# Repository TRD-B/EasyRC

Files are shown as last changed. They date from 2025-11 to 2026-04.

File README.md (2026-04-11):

# EasyRC - open-source RC platform

EasyRC vehicle

Description
---
EasyRC is an easy-to-build platform for creating your own remote-controlled vehicle. The platform includes CAD files for printing an affordable 1:16 scale car as well as a small remote control. Further, it includes the project and production files for the printed circuit boards that are needed to power these devices. Last but not least, it lists all required components in a bill of materials and comes with a complete instruction manual that shows how to print, solder, assemble, program, and adjust everything for running the car. The legacy folder contains data and information from previous revisions of the project.

The idea of this platform is to serve as a starting point for people who are interested in DIY hobby electronics as well as 3D printing, but were reluctant so far due to the initial burdens that are associated with the complexity of these topics. Hence, EasyRC offers a simple start for beginners, but due to its open-source character, it offers full freedom to tweak, redesign, and reprogram all parts of the project.

The 1:16 scale vehicle is designed for indoor use (for the sake of simplicity, it does not encompass suspension) and can be safely operated by kids (maximum speed is 10 km/h but can be set lower within the software). Hence, the project is also a great gift for kids who want to dive into engineering and programming topics, or start with driving a selfmade remote-controlled car and look behind the scenes once they're getting older.

The manual is available in English and German.

Specifications
---
Vehicle:
- Size: 282x125x95 mm³ (LxWxH)
- Scale: 1:16
- Weight: approx. 1 kg (including batteries)
- Microcontroller: ESP32-C3
- Wireless communication: 2.4 GHz (ESP-NOW protocol)
- Motor driver: Pololu DRV8876 (QFN)
- Drive motor: JGA25-370 Brushed DC motor with gearbox (12 V, 1000 U/min)
- Speed: max. 10 km/h
- Steering servo: MG90S metal-gear micro servo
- Power supply: 3x 18650 Li-Ion battery (11.1 V)
- Power consumption: approx. 0.8 W (idle); approx. 3-6 W (driving)

Remote control:
- Size: 80x40x41 mm³ (LxWxH)
- Weight: approx. 125 g (including battery)
- Microcontroller: ESP32-C3
- Wireless communication: 2.4 GHz (ESP-NOW protocol)
- Joystick: Alps 10k (Playstation 4 model)
- Power supply: 1x 18650 Li-Ion battery (3.7 V)
- Power consumption: approx. 0.5 W

Safety information:
---
- Voltage levels are 12 V or less (harmless for humans)
-	Battery connectors are reverse polarity protected
-	Low battery warnings are included
-	The motor automatically stops if the connection to the remote control is lost

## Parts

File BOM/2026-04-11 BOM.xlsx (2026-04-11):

Component | Description | Amount needed | Pieces per unit | Required units | Costs per unit | Costs per piece | Scaled price | Total cost | Link
Motor | Brushed 370 with 1:10 gearbox | 1 | 1 | 1 | 8.49 € | 8.49 € | 8.49 € | 8.49 € | https://www.amazon.de/dp/B07ZKKN226?
Servo | MG90S metal gear micro servo | 1 | 1 | 1 | 4.00 € | 4.00 € | 4.00 € | 4.00 € | https://funduinoshop.com/elektronische-module/elektromotoren-und-zubehoer/elektromotoren/servomotoren/mg90s-metallgetriebe-micro-servo
Battery holder | 3x18650 | 1 | 1 | 1 | 1.87 € | 1.87 € | 1.87 € | 1.87 € | https://funduinoshop.com/werkstatt/stromversorgung/batteriefaecher-und-klemmen/batterriefach-fuer-3x-3-7v-18650-batterien-11-7v-mit-kabel
Battery holder | 1x18650 | 1 | 1 | 1 | 1.06 € | 1.06 € | 1.06 € | 1.06 € | https://funduinoshop.com/werkstatt/stromversorgung/batteriefaecher-und-klemmen/batteriefach-1x-18650-li-ionen-zelle
Battery | Lishen 18650 3.1 Ah | 4 | 10 | 1 | 26.50 € | 2.65 € | 10.60 € | 26.50 € | https://www.pollin.de/p/liion-akku-lishen-lr1865ss-3-6v-3-1ah-273545
Microcontroller | Xiao ESP32-C3 | 2 | 1 | 2 | 5.90 € | 5.90 € | 11.80 € | 11.80 € | https://botland.de/wifi-und-bt-module-esp32/21859-seeed-xiao-esp32-c3-wlan-bluetooth-seeedstudio-113991054.html
On/off switch | Marquardt 1801.1148 | 1 | 1 | 1 | 1.80 € | 1.80 € | 1.80 € | 1.80 € | https://www.reichelt.de/de/de/shop/produkt/wippschalter_ein_-_aus_1_polig_schwarz-257132
On/off switch | Miniature slide switch | 1 | 1 | 1 | 0.48 € | 0.48 € | 0.48 € | 0.48 € | https://www.reichelt.de/de/de/shop/produkt/schiebeschalter-miniatur_loetanschluss_2x_um_sw-19976
Fuse | PTC, ESKA FRG300-16F | 1 | 1 | 1 | 0.47 € | 0.47 € | 0.47 € | 0.47 € | https://www.voelkner.de/products/2682/ESKA-FRG300-16F-FRG300-16F-PTC-Sicherung-Strom-I-H-3A-16V-L-x-B-x-H-7.8-x-3.0-x-19.3mm.html
DC-DC converter | TSR1-2450E | 1 | 1 | 1 | 3.28 € | 3.28 € | 3.28 € | 3.28 € | https://www.voelkner.de/products/3510672/TracoPower-TSR-1-2450E-DC-DC-Wandler-Print-1A-5W-Anzahl-Ausgaenge-1-x-Inhalt-1St..html
Capacitor | Electrolytic, 100µF 25V 6.3mm pitch 2.5mm | 2 | 1 | 2 | 0.25 € | 0.25 € | 0.50 € | 0.50 € | https://www.reichelt.de/de/de/shop/produkt/elko_radial_100_uf_25_v_105_c_low_esr-200027
Capacitor | Electrolytic, 22µF 25V 5mm pitch 2.5mm | 1 | 1 | 1 | 0.25 € | 0.25 € | 0.25 € | 0.25 € | https://www.reichelt.de/de/de/shop/produkt/elko_radial_22_f_25_v_105_c_low_esr_5_x_7_mm_rm_2_5-84588
Buzzer | PB1220PE05Q | 1 | 1 | 1 | 0.50 € | 0.50 € | 0.50 € | 0.50 € | https://www.reichelt.de/de/de/shop/produkt/ac-signalgeber_85db_2048_hz_5_v-360862?search=pb1220&
LED | 5 mm, white | 2 | 1 | 2 | 0.08 € | 0.08 € | 0.16 € | 0.16 € | https://www.reichelt.de/de/de/shop/produkt/led_5_mm_bedrahtet_kaltweiss_15000_mcd_25_-347932
LED | 5 mm, yellow | 4 | 1 | 4 | 0.08 € | 0.08 € | 0.32 € | 0.32 € | https://www.reichelt.de/de/de/shop/produkt/led_5_mm_bedrahtet_gelb_700_mcd_30_-347921
LED | 5 mm, red | 2 | 1 | 2 | 0.08 € | 0.08 € | 0.16 € | 0.16 € | https://www.reichelt.de/de/de/shop/produkt/led_5_mm_bedrahtet_rot_700_mcd_30_-347922
LED | 5 mm, green | 1 | 1 | 1 | 0.08 € | 0.08 € | 0.08 € | 0.08 € | https://www.reichelt.de/de/de/shop/produkt/led_5_mm_bedrahtet_gruen_2500_mcd_30_-347919
Motor driver | Pololu DRV8876 QFN | 1 | 1 | 1 | 6.50 € | 6.50 € | 6.50 € | 6.50 € | https://botland.de/motortreiber-module/21361-drv8876-qfn-einkanal-treiber-37-v-11-a-pololu-4037.html
MOSFET | IRLU 024N | 6 | 1 | 6 | 0.46 € | 0.46 € | 2.76 € | 2.76 € | https://www.reichelt.de/de/de/shop/produkt/mosfet_n-ch_55v_17a_0_065r_to-251aa-90365
Zener diode | Semtech ZD 8.2 | 1 | 1 | 1 | 0.05 € | 0.05 € | 0.05 € | 0.05 € | https://www.reichelt.de/de/de/shop/produkt/zenerdiode_8_2_v_1_w_do-204al_do41-23101
Schottky diode | 1N 5817 | 1 | 1 | 1 | 0.10 € | 0.10 € | 0.10 € | 0.10 € | https://www.reichelt.de/de/de/shop/produkt/schottkydiode_20_v_1_a_do-41-376347
Resistor | 330Ohm 0207 | 1 | 1 | 1 | 0.07 € | 0.07 € | 0.07 € | 0.07 € | https://www.reichelt.de/de/de/shop/produkt/widerstand_metallschicht_330_ohm_0207_0_6_w_1_-11733
Resistor | 470Ohm 0207 | 16 | 1 | 16 | 0.07 € | 0.07 € | 1.12 € | 1.12 € | https://www.reichelt.de/de/de/shop/produkt/widerstand_metallschicht_470_ohm_0207_0_6_w_1_-11826
Resistor | 1kOhm 0207 | 4 | 1 | 1 | 0.07 € | 0.07 € | 0.28 € | 0.07 € | https://www.reichelt.de/de/de/shop/produkt/widerstand_metallschicht_1_00_kohm_0207_0_6_w_1_-11403
Resistor | 10kOhm 0207 | 1 | 1 | 1 | 0.07 € | 0.07 € | 0.07 € | 0.07 € | https://www.reichelt.de/de/de/shop/produkt/widerstand_metallschicht_10_0_kohm_0207_0_6_w_1_-11449
Resistor | 22kOhm 0207 | 3 | 1 | 1 | 0.07 € | 0.07 € | 0.21 € | 0.07 € | https://www.reichelt.de/de/de/shop/produkt/widerstand_metallschicht_22_0_kohm_0207_0_6_w_1_-11622
Resistor | 33kOhm 0207 | 2 | 1 | 2 | 0.07 € | 0.07 € | 0.14 € | 0.14 € | https://www.reichelt.de/de/de/shop/produkt/widerstand_metallschicht_33_0_kohm_0207_0_6_w_1_-11730
Resistor | 100kOhm 0207 | 2 | 1 | 1 | 0.07 € | 0.07 € | 0.14 € | 0.07 € | https://www.reichelt.de/de/de/shop/produkt/widerstand_metallschicht_100_kohm_0207_0_6_w_1_-11458
Joystick | ALPS PS4 Joystick | 1 | 1 | 1 | 2.90 € | 2.90 € | 2.90 € | 2.90 € | https://www.retroretter.de/products/as_ps4_white_alps_10k
Pin header | W+P 10-pin angled | 1 | 2 | 1 | 0.36 € | 0.18 € | 0.18 € | 0.36 € | https://www.reichelt.de/de/de/shop/produkt/stiftleiste_rm_2_54mm_gewinkelt_1-reihig_10-polig-330991
Socket strip | mpe 7-pin | 4 | 1 | 6 | 0.31 € | 0.31 € | 1.24 € | 1.86 € | https://www.reichelt.de/de/de/shop/produkt/buchsenleisten_2_54_mm_1x07_gerade-119916
Socket strip | 10-pin (5 mm height) | 2 | 1 | 1 | 0.75 € | 0.75 € | 1.50 € | 0.75 € | https://www.reichelt.de/de/de/shop/produkt/10pol_buchsenleiste_gerade_rm_2_54-6070
Pin header | mpe 1x20-pin | 5 | 5 | 1 | 0.35 € | 0.07 € | 0.35 € | 0.35 € | https://www.reichelt.de/de/de/shop/produkt/stiftleisten_2_54_mm_1x20_gerade-119888
Pin header | mpe 2x20-pin | 4 | 4 | 1 | 0.69 € | 0.17 € | 0.69 € | 0.69 € | https://www.reichelt.de/de/de/shop/produkt/stiftleisten_2_54_mm_2x20_gerade-119900
Crimp set | Dupont 610 parts | 15 | 100 | 1 | 9.75 € | 0.10 € | 1.46 € | 9.75 € | https://www.reichelt.de/de/de/shop/produkt/entwicklerboards_-_dupont-crimp-set_610-teilig-279901
Wire | 0.25 mm², black, 25m | 4 | 25 | 1 | 4.70 € | 0.19 € | 0.75 € | 4.70 € | https://www.pollin.de/p/rautronic-schaltlitze-liyv-0-25-mm2-25-m-schwarz-560118
Wire | 0.25 mm², red, 25m | 4 | 25 | 1 | 4.70 € | 0.19 € | 0.75 € | 4.70 € | https://www.pollin.de/p/rautronic-schaltlitze-liyv-0-25-mm2-25-m-rot-560048
Ball bearing | 608ZZ 8x22x7 | 4 | 50 | 1 | 9.99 € | 0.20 € | 0.80 € | 9.99 € | https://www.amazon.de/Rillenkugellager-Carbonstahl-Pr%C3%A4zisionslager-Skateboards-Rollerblades/dp/B0F28Q2LCV/
Ball bearing | 605ZZ 5x14x5 | 4 | 30 | 1 | 8.99 € | 0.30 € | 1.20 € | 8.99 € | https://www.amazon.de/QUARKZMAN-Rillenkugel-Bohrung-Karbonstahl-Abgeschirmt/dp/B0CL4XKFW7/?th=1
Ball bearing | 6802ZZ 15x24x5 | 2 | 10 | 1 | 6.72 € | 0.67 € | 1.34 € | 6.72 € | https://www.motedis.com/de/Rillenkugellager-6802-2Z-15x24x5
Filament | PETG, black | 400 | 1000 | 1 | 32.99 € | 0.03 € | 13.20 € | 32.99 € | https://www.prusa3d.com/product/prusament-petg-jet-black-1kg/
Filament | PETG, red | 250 | 1000 | 1 | 32.99 € | 0.03 € | 8.25 € | 32.99 € | https://www.prusa3d.com/product/prusament-petg-lipstick-red-1kg/
Filament | TPU, 82A | 35 | 500 | 1 | 32.99 € | 0.07 € | 2.31 € | 32.99 € | https://www.3djake.de/recreus/filaflex-black
Screw | M3x8 | 29 | 100 | 1 | 3.58 € | 0.04 € | 1.04 € | 3.58 € | https://shop.der-schraubenladen.de/DIN-912-ISO-4762-Zylinderschraube-Innensechskant-Edelstahl-A2/SW11250.70
Screw | M3x10 countersunk | 3 | 1000 | 1 | 19.35 € | 0.02 € | 0.06 € | 19.35 € | https://shop.der-schraubenladen.de/DIN-7991-ISO-10642-Senkschraube-Innensechskant-Edelstahl-A2/SW11501.23
Screw | M3x16 | 11 | 100 | 1 | 4.37 € | 0.04 € | 0.48 € | 4.37 € | https://shop.der-schraubenladen.de/DIN-912-ISO-4762-Zylinderschraube-Innensechskant-Edelstahl-A2/SW11250.74
Screw | M3x20 | 8 | 100 | 1 | 5.54 € | 0.06 € | 0.44 € | 5.54 € | https://shop.der-schraubenladen.de/DIN-912-ISO-4762-Zylinderschraube-Innensechskant-Edelstahl-A2/SW11250.76
Screw | M3x30 | 21 | 100 | 1 | 7.57 € | 0.08 € | 1.59 € | 7.57 € | https://shop.der-schraubenladen.de/DIN-912-ISO-4762-Zylinderschraube-Innensechskant-Edelstahl-A2/SW11250.79
Hex nut | M3 | 64 | 500 | 1 | 10.76 € | 0.02 € | 1.38 € | 10.76 € | https://shop.der-schraubenladen.de/DIN-934-ISO-4032-Sechskantmutter-Edelstahl-A2/SW11410.19
PCB | JLCPCB | 1 | 5 | 1 | 8.00 € | 1.60 € | 1.60 € | 8.00 € | https://jlcpcb.com/
PCB | JLCPCB | 1 | 5 | 1 | 8.00 € | 1.60 € | 1.60 € | 8.00 € | https://jlcpcb.com/
 |  |  |  |  |  |  | Scaled | Prototype
Total costs |  |  |  |  |  |  | 102.37 € | 290.64 €

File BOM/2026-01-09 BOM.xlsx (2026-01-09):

Component | Description | Amount needed | Pieces per unit | Required units | Costs per unit | Costs per piece | Scaled price | Total cost | Link
Motor | Brushed 370 with 1:10 gearbox | 1 | 1 | 1 | 8.49 | 8.49 | 8.49 | 8.49 | https://www.amazon.de/dp/B07ZKKN226?
Servo | MG90S metal gear micro servo | 1 | 1 | 1 | 4 | 4 | 4 | 4 | https://funduinoshop.com/elektronische-module/elektromotoren-und-zubehoer/elektromotoren/servomotoren/mg90s-metallgetriebe-micro-servo
Battery holder | 3x18650 | 1 | 1 | 1 | 1.87 | 1.87 | 1.87 | 1.87 | https://funduinoshop.com/werkstatt/stromversorgung/batteriefaecher-und-klemmen/batterriefach-fuer-3x-3-7v-18650-batterien-11-7v-mit-kabel
Battery holder | 1x18650 | 1 | 1 | 1 | 1.06 | 1.06 | 1.06 | 1.06 | https://funduinoshop.com/werkstatt/stromversorgung/batteriefaecher-und-klemmen/batteriefach-1x-18650-li-ionen-zelle
Battery | Lishen 18650 3.1 Ah | 4 | 10 | 1 | 26.5 | 2.65 | 10.6 | 26.5 | https://www.pollin.de/p/liion-akku-lishen-lr1865ss-3-6v-3-1ah-273545
Microcontroller | Xiao ESP32-C3 | 2 | 1 | 2 | 5.9 | 5.9 | 11.8 | 11.8 | https://botland.de/wifi-und-bt-module-esp32/21859-seeed-xiao-esp32-c3-wlan-bluetooth-seeedstudio-113991054.html
On/off switch | Marquardt 1801.1148 | 1 | 1 | 1 | 1.8 | 1.8 | 1.8 | 1.8 | https://www.reichelt.de/de/de/shop/produkt/wippschalter_ein_-_aus_1_polig_schwarz-257132
On/off switch | Miniature slide switch | 1 | 1 | 1 | 0.48 | 0.48 | 0.48 | 0.48 | https://www.reichelt.de/de/de/shop/produkt/schiebeschalter-miniatur_loetanschluss_2x_um_sw-19976
Fuse | PTC, 1.5A | 1 | 1 | 1 | 0.76 | 0.76 | 0.76 | 0.76 | https://www.reichelt.de/de/de/shop/produkt/ptc-sicherung_smd_1812_24v_1_5a_rueckstellend-279366
DC-DC converter | TSR1-2450E | 1 | 1 | 1 | 3.99 | 3.99 | 3.99 | 3.99 | https://www.reichelt.de/de/de/shop/produkt/dc_dc_converter_tsr_1e_1_a_7-36_5_0_vdc_sip-3-288648
Capacitor | Electrolytic, 100µF 25V 6.3mm pitch 2.5mm | 2 | 1 | 2 | 0.25 | 0.25 | 0.5 | 0.5 | https://www.reichelt.de/de/de/shop/produkt/elko_radial_100_uf_25_v_105_c_low_esr-200027
Buzzer | PB1220PE05Q | 1 | 1 | 1 | 0.5 | 0.5 | 0.5 | 0.5 | https://www.reichelt.de/de/de/shop/produkt/ac-signalgeber_85db_2048_hz_5_v-360862?search=pb1220&
LED | 5 mm, white | 2 | 1 | 2 | 0.08 | 0.08 | 0.16 | 0.16 | https://www.reichelt.de/de/de/shop/produkt/led_5_mm_bedrahtet_kaltweiss_15000_mcd_25_-347932
LED | 5 mm, yellow | 4 | 1 | 4 | 0.08 | 0.08 | 0.32 | 0.32 | https://www.reichelt.de/de/de/shop/produkt/led_5_mm_bedrahtet_gelb_700_mcd_30_-347921
LED | 5 mm, red | 2 | 1 | 2 | 0.08 | 0.08 | 0.16 | 0.16 | https://www.reichelt.de/de/de/shop/produkt/led_5_mm_bedrahtet_rot_700_mcd_30_-347922
LED | 5 mm, green | 1 | 1 | 1 | 0.08 | 0.08 | 0.08 | 0.08 | https://www.reichelt.de/de/de/shop/produkt/led_5_mm_bedrahtet_gruen_2500_mcd_30_-347919
Motor driver | Pololu DRV8876 QFN | 1 | 1 | 1 | 6.5 | 6.5 | 6.5 | 6.5 | https://botland.de/motortreiber-module/21361-drv8876-qfn-einkanal-treiber-37-v-11-a-pololu-4037.html
MOSFET | IRLML6344 | 6 | 1 | 6 | 0.25 | 0.25 | 1.5 | 1.5 | https://www.reichelt.de/de/de/shop/produkt/mosfet_n-ch_30v_5a_0_029r_sot-23-132147
Zener diode | CDIL SMD ZD 8.2 | 1 | 1 | 1 | 0.04 | 0.04 | 0.04 | 0.04 | https://www.reichelt.de/de/de/shop/produkt/zenerdiode_8_2_v_0_35_w_sot-23-18926
Capacitor | ceramic, 22µF 10V 1206 | 2 | 1 | 2 | 0.26 | 0.26 | 0.52 | 0.52 | https://www.reichelt.de/de/de/shop/produkt/smd-vielschichtkondensator_g1206_-_22_f_10v-89742
Capacitor | ceramic 100nF 50V 0805 | 1 | 1 | 1 | 0.03 | 0.03 | 0.03 | 0.03 | https://www.reichelt.de/de/de/shop/produkt/smd-kerko_0805_100_nf_50v_10_x7r_mlcc-346808
Resistor | 330Ohm 0805 | 1 | 1 | 1 | 0.02 | 0.02 | 0.02 | 0.02 | https://www.reichelt.de/de/de/shop/produkt/smd-widerstand_0805_220_ohm_125_mw_1_-346599
Resistor | 470Ohm 0805 | 16 | 1 | 16 | 0.02 | 0.02 | 0.32 | 0.32 | https://www.reichelt.de/de/de/shop/produkt/smd-widerstand_0805_470_ohm_125_mw_1_-346619
Resistor | 1kOhm 0805 | 4 | 1 | 1 | 0.02 | 0.02 | 0.08 | 0.02 | https://www.reichelt.de/de/de/shop/produkt/smd-widerstand_0805_1_kohm_125_mw_1_-346593
Resistor | 22kOhm 0805 | 3 | 1 | 1 | 0.02 | 0.02 | 0.06 | 0.02 | https://www.reichelt.de/de/de/shop/produkt/smd-widerstand_0805_22_kohm_125_mw_1_-346600
Resistor | 10kOhm 0805 | 1 | 1 | 1 | 0.02 | 0.02 | 0.02 | 0.02 | https://www.reichelt.de/de/de/shop/produkt/smd-widerstand_0805_10_kohm_125_mw_1_-346579
Resistor | 33kOhm 0805 | 2 | 1 | 2 | 0.02 | 0.02 | 0.04 | 0.04 | https://www.reichelt.de/de/de/shop/produkt/smd-widerstand_0805_33_kohm_125_mw_1_-346610
Resistor | 100kOhm 0805 | 2 | 1 | 1 | 0.02 | 0.02 | 0.04 | 0.02 | https://www.reichelt.de/de/de/shop/produkt/smd-widerstand_0805_100_kohm_125_mw_1_-346577
Joystick | ALPS PS4 Joystick | 1 | 1 | 1 | 2.9 | 2.9 | 2.9 | 2.9 | https://www.retroretter.de/products/as_ps4_white_alps_10k
Pin header | W+P 10-pin angled | 1 | 2 | 1 | 0.36 | 0.18 | 0.18 | 0.36 | https://www.reichelt.de/de/de/shop/produkt/stiftleiste_rm_2_54mm_gewinkelt_1-reihig_10-polig-330991
Socket strip | mpe 7-pin | 4 | 1 | 6 | 0.31 | 0.31 | 1.24 | 1.86 | https://www.reichelt.de/de/de/shop/produkt/buchsenleisten_2_54_mm_1x07_gerade-119916
Socket strip | 10-pin (5 mm height) | 2 | 1 | 1 | 0.75 | 0.75 | 1.5 | 0.75 | https://www.reichelt.de/de/de/shop/produkt/10pol_buchsenleiste_gerade_rm_2_54-6070
Pin header | mpe 1x20-pin | 5 | 5 | 1 | 0.35 | 0.07 | 0.35 | 0.35 | https://www.reichelt.de/de/de/shop/produkt/stiftleisten_2_54_mm_1x20_gerade-119888
Pin header | mpe 2x20-pin | 4 | 4 | 1 | 0.69 | 0.1725 | 0.69 | 0.69 | https://www.reichelt.de/de/de/shop/produkt/stiftleisten_2_54_mm_2x20_gerade-119900
Jumper | 2.54 mm Jumper | 1 | 1 | 1 | 0.02 | 0.02 | 0.02 | 0.02 | https://www.reichelt.de/de/de/shop/produkt/kurzschlussbruecke_schwarz_rm_2_54-9017
Crimp set | Dupont 610 parts | 15 | 100 | 1 | 9.75 | 0.0975 | 1.4625 | 9.75 | https://www.reichelt.de/de/de/shop/produkt/entwicklerboards_-_dupont-crimp-set_610-teilig-279901
Wire | 0.25 mm², black, 25m | 4 | 25 | 1 | 4.7 | 0.188 | 0.752 | 4.7 | https://www.pollin.de/p/rautronic-schaltlitze-liyv-0-25-mm2-25-m-schwarz-560118
Wire | 0.25 mm², red, 25m | 4 | 25 | 1 | 4.7 | 0.188 | 0.752 | 4.7 | https://www.pollin.de/p/rautronic-schaltlitze-liyv-0-25-mm2-25-m-rot-560048
Ball bearing | 608ZZ 8x22x7 | 4 | 50 | 1 | 9.99 | 0.1998 | 0.7992 | 9.99 | https://www.amazon.de/Rillenkugellager-Carbonstahl-Pr%C3%A4zisionslager-Skateboards-Rollerblades/dp/B0F28Q2LCV/
Ball bearing | 605ZZ 5x14x5 | 4 | 30 | 1 | 8.99 | 0.2996666667 | 1.198666667 | 8.99 | https://www.amazon.de/QUARKZMAN-Rillenkugel-Bohrung-Karbonstahl-Abgeschirmt/dp/B0CL4XKFW7/?th=1
Ball bearing | 6802ZZ 15x24x5 | 2 | 10 | 1 | 6.72 | 0.672 | 1.344 | 6.72 | https://www.motedis.com/de/Rillenkugellager-6802-2Z-15x24x5
Filament | PETG, black | 400 | 1000 | 1 | 32.99 | 0.03299 | 13.196 | 32.99 | https://www.prusa3d.com/product/prusament-petg-jet-black-1kg/
Filament | PETG, red | 250 | 1000 | 1 | 32.99 | 0.03299 | 8.2475 | 32.99 | https://www.prusa3d.com/product/prusament-petg-lipstick-red-1kg/
Filament | TPU, 82A | 35 | 500 | 1 | 32.99 | 0.06598 | 2.3093 | 32.99 | https://www.3djake.de/recreus/filaflex-black
Screw | M3x8 | 29 | 100 | 1 | 3.58 | 0.0358 | 1.0382 | 3.58 | https://shop.der-schraubenladen.de/DIN-912-ISO-4762-Zylinderschraube-Innensechskant-Edelstahl-A2/SW11250.70
Screw | M3x10 countersunk | 3 | 1000 | 1 | 19.35 | 0.01935 | 0.05805 | 19.35 | https://shop.der-schraubenladen.de/DIN-7991-ISO-10642-Senkschraube-Innensechskant-Edelstahl-A2/SW11501.23
Screw | M3x12 | 4 | 100 | 1 | 3.9 | 0.039 | 0.156 | 3.9 | https://shop.der-schraubenladen.de/DIN-912-ISO-4762-Zylinderschraube-Innensechskant-Edelstahl-A2/SW11250.72
Screw | M3x16 | 7 | 100 | 1 | 4.37 | 0.0437 | 0.3059 | 4.37 | https://shop.der-schraubenladen.de/DIN-912-ISO-4762-Zylinderschraube-Innensechskant-Edelstahl-A2/SW11250.74
Screw | M3x20 | 6 | 100 | 1 | 5.54 | 0.0554 | 0.3324 | 5.54 | https://shop.der-schraubenladen.de/DIN-912-ISO-4762-Zylinderschraube-Innensechskant-Edelstahl-A2/SW11250.76
Screw | M3x22 | 2 | 100 | 1 | 6 | 0.06 | 0.12 | 6 | https://shop.der-schraubenladen.de/DIN-912-ISO-4762-Zylinderschraube-Innensechskant-Edelstahl-A2/SW11250.77
Screw | M3x30 | 17 | 100 | 1 | 7.57 | 0.0757 | 1.2869 | 7.57 | https://shop.der-schraubenladen.de/DIN-912-ISO-4762-Zylinderschraube-Innensechskant-Edelstahl-A2/SW11250.79
Screw | M3x35 | 2 | 100 | 1 | 8.66 | 0.0866 | 0.1732 | 8.66 | https://shop.der-schraubenladen.de/DIN-912-ISO-4762-Zylinderschraube-Innensechskant-Edelstahl-A2/SW11250.80
Screw | M3x40 | 2 | 100 | 1 | 9.69 | 0.0969 | 0.1938 | 9.69 | https://shop.der-schraubenladen.de/DIN-912-ISO-4762-Zylinderschraube-Innensechskant-Edelstahl-A2/SW11250.81
Hex nut | M3 | 64 | 500 | 1 | 10.76 | 0.02152 | 1.37728 | 10.76 | https://shop.der-schraubenladen.de/DIN-934-ISO-4032-Sechskantmutter-Edelstahl-A2/SW11410.19
PCB | JLCPCB | 1 | 5 | 1 | 8 | 1.6 | 1.6 | 8 | https://jlcpcb.com/
PCB | JLCPCB | 1 | 5 | 1 | 8 | 1.6 | 1.6 | 8 | https://jlcpcb.com/
 |  |  |  |  |  |  | Scaled | Prototype
Total costs |  |  |  |  |  |  | 100.9228967 | 317.69

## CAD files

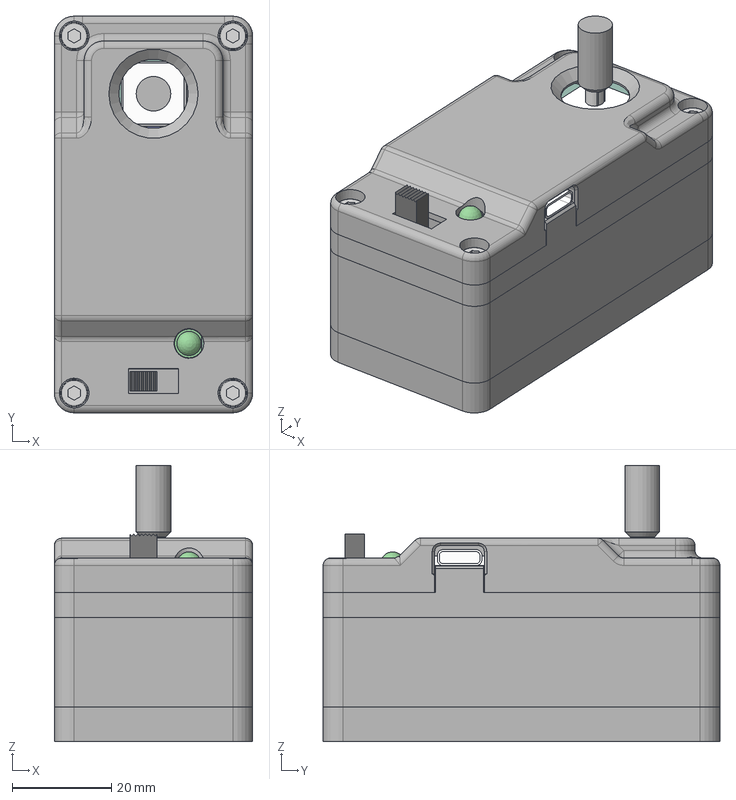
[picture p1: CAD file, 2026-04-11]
CAD files/Assembly/Easy RC remote control.step
40.0 x 80.0 x 55.6 mm
18650 1-cell holder v1
M3x10 countersunk_1
M3x8 screw_2 x 2
M3 nut_7 x 7
M3x30 screw_1 x 4
Remote control lower intermediate frame
Remote control upper intermediate frame
Remote control bottom
Remote control battery cover
Remote control joystick extension
Remote control top
R_Axial_DIN0207_L6.3mm_D2.5mm_P2.54mm_Vertical x 5
Seeed Xiao ESP32-C3
TO-251-3_Vertical
PinHeader_1x04_P2.54mm_Horizontal
PS5 Joystick
Wentronic S166 slide switch
LED_D5.0mm
Easy RC Tx V1.2_pad
Easy RC Tx V1.2_silkscreen
Easy RC Tx V1.2_soldermask
Easy RC Tx V1.2_PCB
Pin header x 2
18650 LiIon v1

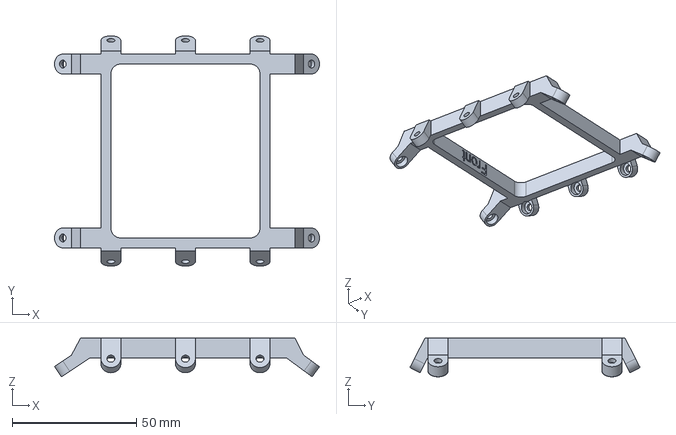
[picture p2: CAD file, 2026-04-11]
CAD files/Car/Window holder.step
106.7 x 92.7 x 15.6 mm

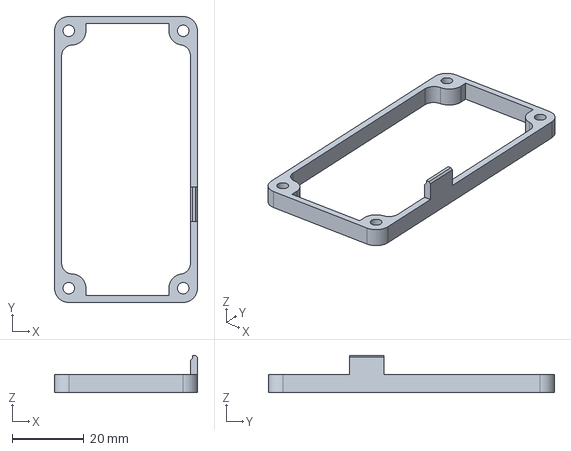
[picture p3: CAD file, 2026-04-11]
CAD files/Remote control/Remote control upper intermediate frame.step
40.0 x 80.0 x 10.4 mm

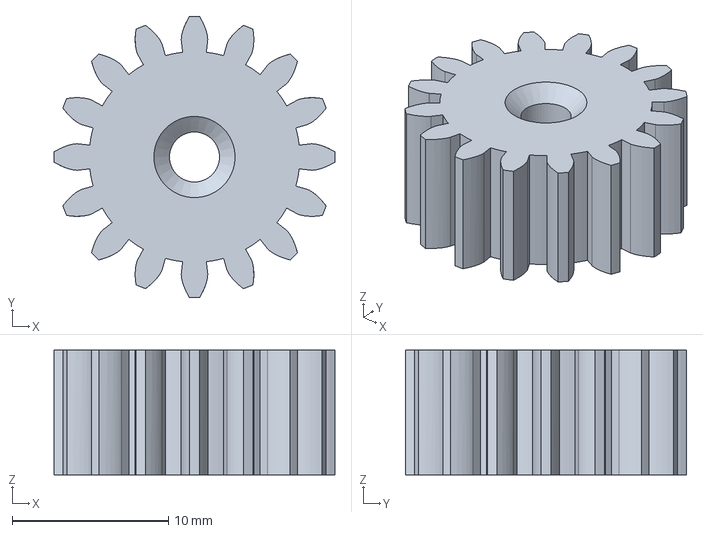
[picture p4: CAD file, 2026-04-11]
CAD files/Car/16 teeth gear.step
18.0 x 18.0 x 8.00 mm

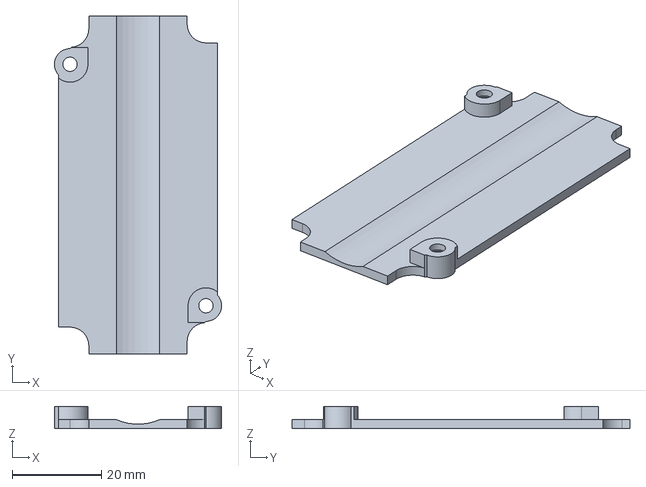
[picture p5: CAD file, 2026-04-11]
CAD files/Remote control/Remote control battery cover.step
37.4 x 75.6 x 5.00 mm

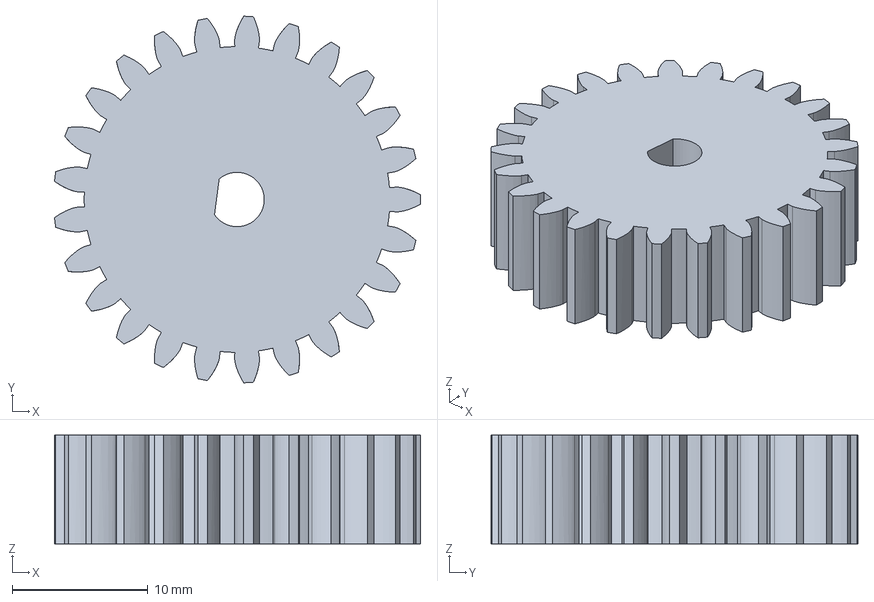
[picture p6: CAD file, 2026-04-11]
CAD files/Car/25 teeth gear.step
26.9 x 27.0 x 8.00 mm

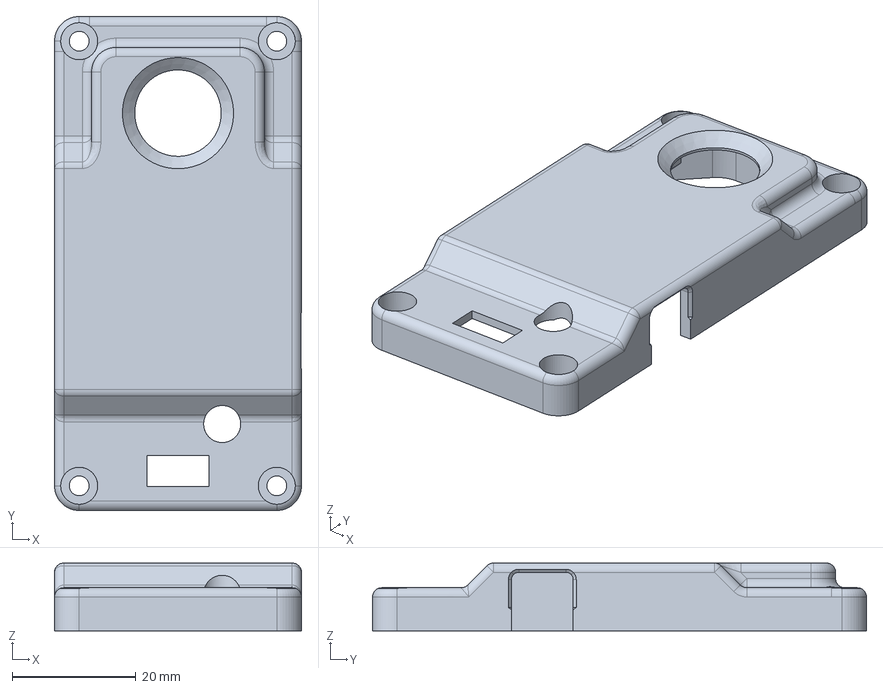
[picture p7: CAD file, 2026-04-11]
CAD files/Remote control/Remote control top.step
40.0 x 80.0 x 11.0 mm

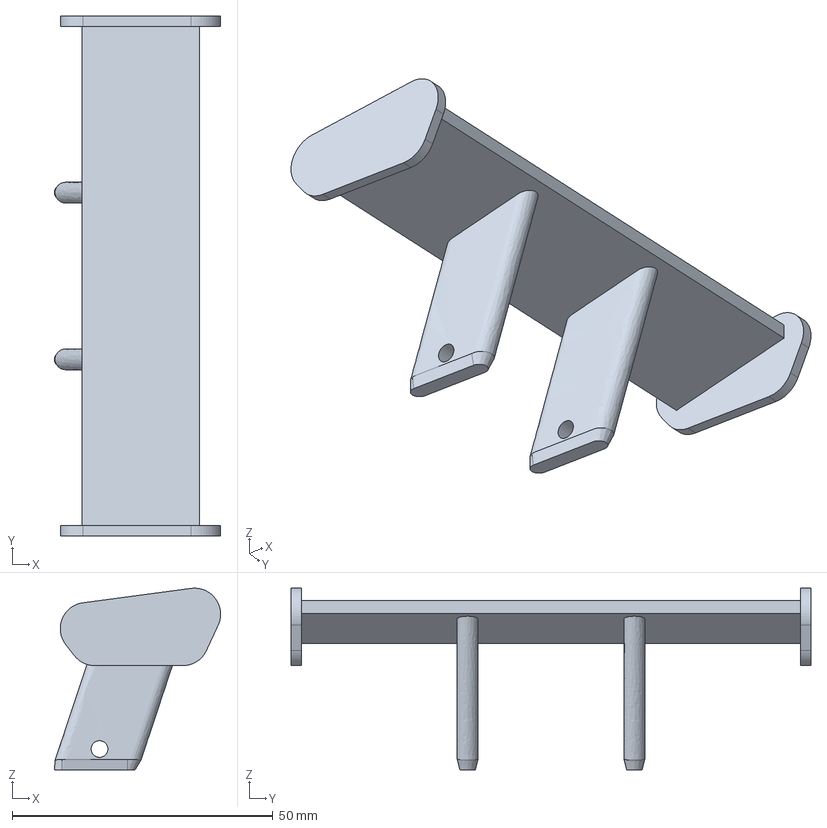
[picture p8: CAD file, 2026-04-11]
CAD files/Car/Rear wing.step
31.9 x 99.8 x 34.9 mm

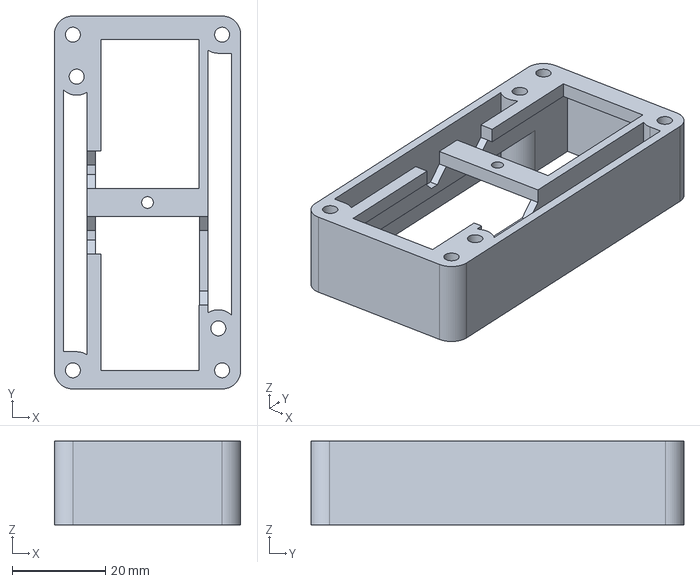
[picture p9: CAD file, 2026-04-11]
CAD files/Remote control/Remote control lower intermediate frame.step
40.0 x 80.0 x 18.0 mm

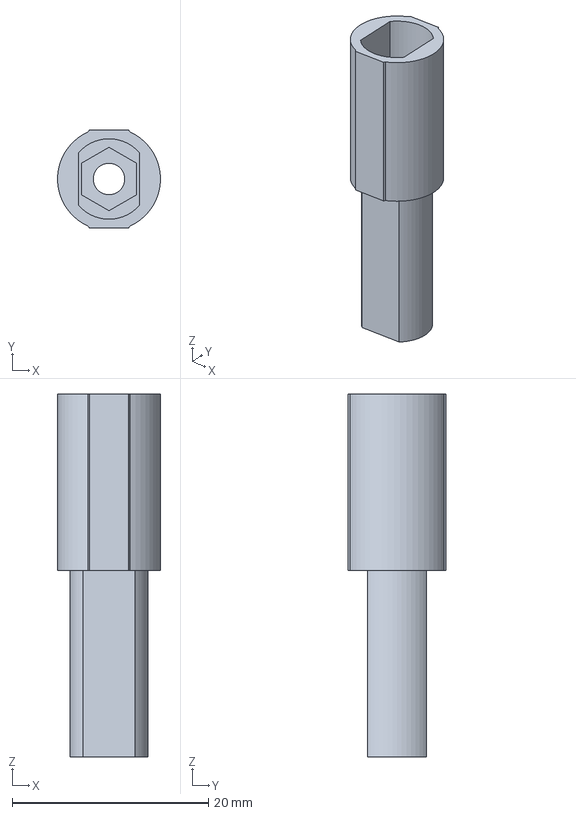
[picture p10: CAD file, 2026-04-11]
CAD files/Car/Right rear axle TPU.step
10.5 x 10.0 x 37.0 mm

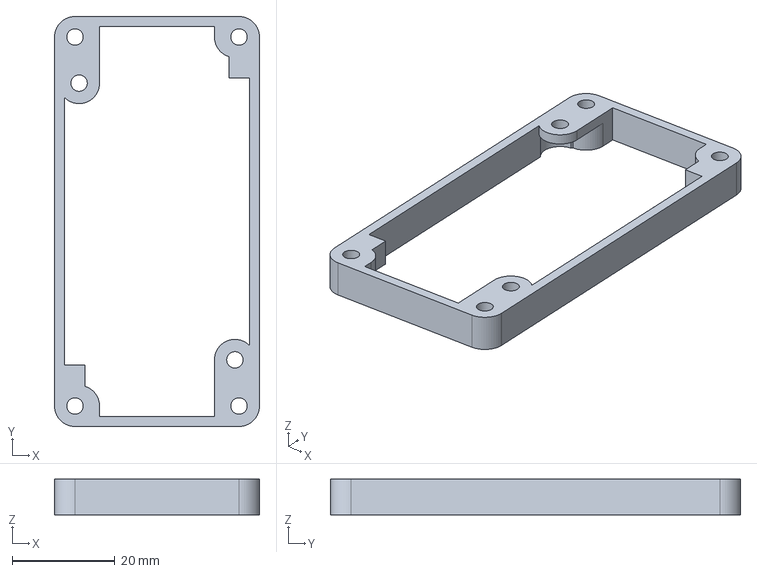
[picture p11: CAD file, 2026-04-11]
CAD files/Remote control/Remote control bottom.step
40.0 x 80.0 x 7.00 mm

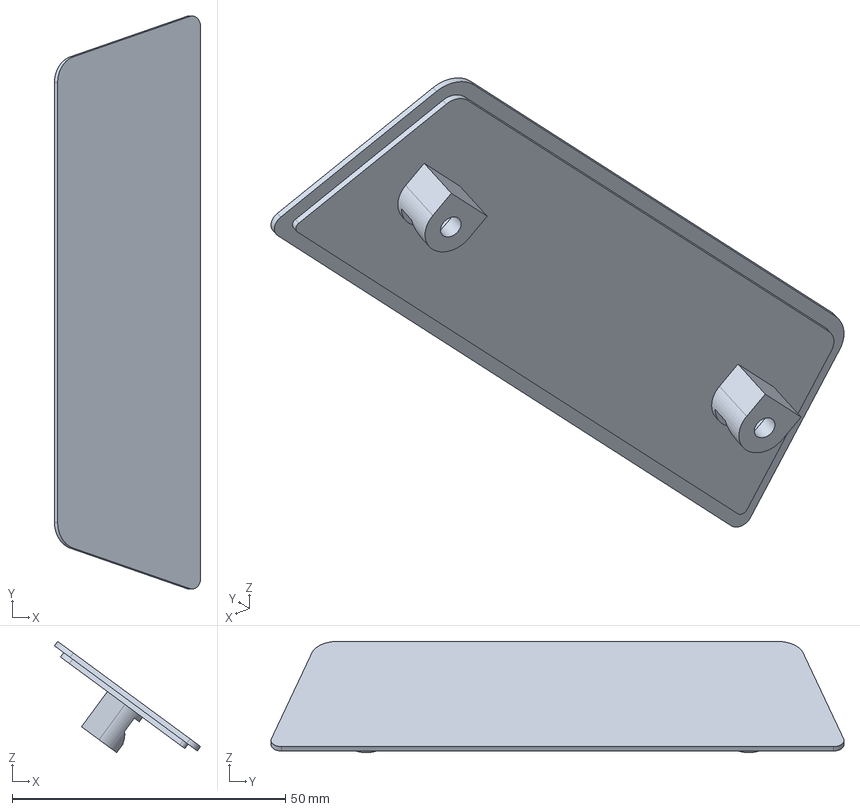
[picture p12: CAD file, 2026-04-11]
CAD files/Car/Rear window.step
26.8 x 104.9 x 20.4 mm

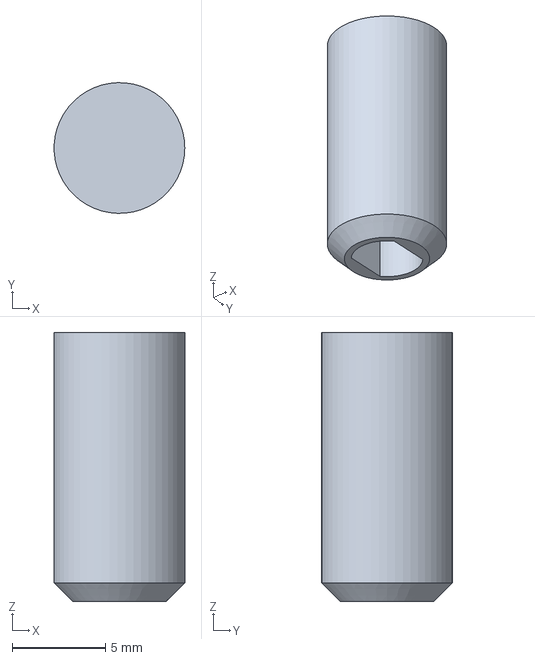
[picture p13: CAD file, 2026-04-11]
CAD files/Remote control/Remote control joystick extension.step
6.99 x 7.00 x 14.4 mm

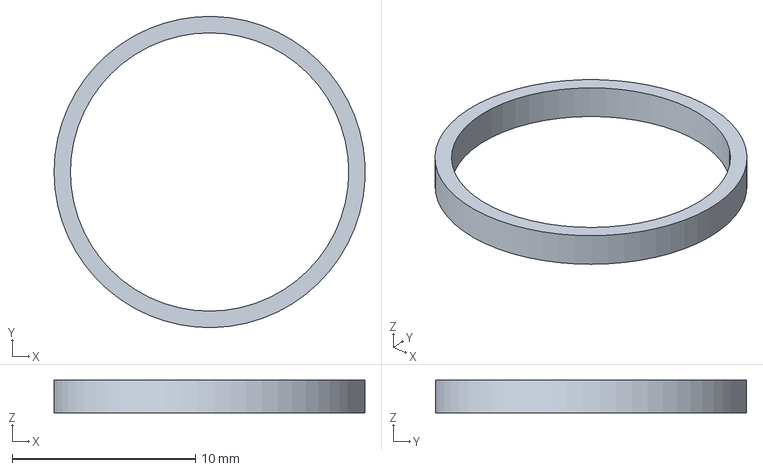
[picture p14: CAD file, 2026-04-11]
CAD files/Car/Differential spacer ring.step
17.0 x 17.0 x 1.80 mm

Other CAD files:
CAD files/Car/Right rear LED insert.step
CAD files/Car/Servo horn attachment large TPU.step
CAD files/Car/Chassis top.step
CAD files/Car/Left rear LED insert.step
CAD files/Car/10 teeth crown gear.step
CAD files/Car/10teeth crown gear.step
CAD files/Car/15 teeth crown gear.step
CAD files/Car/15teeth crown gear.step
CAD files/Car/16 teeth bearing mount.step
CAD files/Car/24 teeth gear.step
CAD files/Car/Battery lid.step
CAD files/Car/Chassis bottom.step
CAD files/Car/Chassis securing bracket.step
CAD files/Car/Differential case.step
CAD files/Car/Differential spacer.step
CAD files/Car/Front LED insert.step
CAD files/Car/Front body.step
CAD files/Car/Front bumper.step
CAD files/Car/Front light clamp.step
CAD files/Car/Front rim locking ring.step
CAD files/Car/Front rim spacer.step
CAD files/Car/Front rim.step
CAD files/Car/Front wheel mount spacer.step
CAD files/Car/Front window.step
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

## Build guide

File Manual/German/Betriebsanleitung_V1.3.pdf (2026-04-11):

# EasyRC – Open Source Fernsteuerungsplattform

## Betriebsanleitung

Version 1.3; Stand: 11.04.2026

2

## Inhaltsverzeichnis

1. Hinweise und Spezifikationen | 4
1.1 | Sicherheitshinweise | 4
1.2 | Spezifikationen der EasyRC-Plattform | 5
2. Teilelisten | 6
2.1 | Elektronikbauteile | 6
2.2 | Metallbauteile | 8
2.3 | Gedruckte Bauteile | 9
3. Elektronik | 16
3.1 | Einführung in die Elektronik | 16
3.2 | Fertigung und Bestückung der Leiterplatten | 17
3.3 | Crimpen und Verlöten der Elektronikbauteile | 18
3.4 | Komponentenliste | 19
3.5 | Übersicht Fernsteuerungselektronik | 22
3.6 | Übersicht Fahrzeugelektronik | 25
4. Bauanleitung Fernsteuerung und Fahrzeug | 31
4.1 | Fernbedienung | 35
4.2 | Antriebsstrang und Hinterräder | 41
4.3 | Vorderräder und Lenkung | 51
4.4 | Finalisierung Chassis | 58
4.5 | Karosserie | 65
5. Programmierung | 73
5.1 | Installation Arduino IDE | 73
5.2 | Mögliche und benötigte Code-Modifikationen | 75
5.3 | Programmieren der Microcontroller | 77
6. Code der Microcontroller | 79
6.1 | Fernsteuerung | 79
6.2 | Fahrzeug | 80
7. Erste Schritte und Bedienung des Fahrzeugs | 82
7.1 | Batterien einsetzen und Geräte anschalten | 82
7.2 | Lenkung fertig montieren | 83
7.3 | Fahrzeug fertig montieren | 85
7.4 | Steuerungsprinzip und Funktionen des Fahrzeugs | 86
7.5 | Trimmung der Lenkung | 87
7.6 | Feintuning der Fahreigenschaften | 88

3

8. Mögliche Fehler und Lösungsansätze | 89
9. Anhang | 90
9.1 | Änderung der Geräte-Adresse der EasyRC-Plattform | 90
9.2 | Änderung des Funkkanals der EasyRC-Plattform | 91
10. | Noch umzusetzende Verbesserungen | 92
11. | Impressum | 93

4

## 1. Hinweise und Spezifikationen

### 1.1 Sicherheitshinweise

EasyRC ist eine open-source-Plattform für drahtlos ferngesteuerte Modellfahrzeuge, die als Bausatz aus 3D-gedruckten Bauteilen montiert werden. Das Benutzerhandbuch muss vor dem Zusammenbau und der Inbetriebnahme vollständig gelesen und verstanden werden, um Gefahrenquellen zu erkennen und Verletzungen oder Schäden zu vermeiden.
Für ferngesteuerte Modellfahrzeuge gilt grundsätzlich, dass diese nicht im öentlichen Straßenverkehr bewegt werden dürfen. Bei ferngesteuerten Modellen besteht die Gefahr, dass der Steuernde die Kontrolle verliert, wenn die Drahtlosverbindung durch Überschreiten der maximalen Übertragungsreichweite oder Interferenzen gestört wird. EasyRC beinhaltet dafür eine Sicherheitsroutine, die beim Ausbleiben von Funksignalen der Fernsteuerung für wenigstens eine Sekunde die Motoren deaktiviert (die Fernsteuerung überträgt pro Sekunde 20 Datenpakete an das Modellfahrzeug, sodass diese Sicherung nicht durch einzelne verlorene Datenpakete ausgelöst werden kann). Diese Sicherheitsroutine bleibt jedoch funktionslos bei Störsignalen, die vom Modellfahrzeug fälschlicherweise als Signal der Fernsteuerung interpretiert werden. Dafür prüft das Modellfahrzeug die individuelle Geräte-Adresse (MAC) der Fernsteuerung, die mit jedem Datenpaket gesendet wird. Nur wenn diese mit der intern gespeicherten Geräte-Adresse der gekoppelten Fernsteuerung übereinstimmt, wird das Datenpaket weiterverarbeitet. Deshalb ist es beim gleichzeitigen Betrieb mehrerer EasyRC-Modelle wichtig, dass jedes mit einer anderen Geräte-Adresse programmiert wird, sodass jede Fernsteuerung spezifisch nur ein Fahrzeug steuert. Die Drahtlosverbindung basiert auf einer Funkfrequenz von 2,4 GHz, in der auch herkömmliches WLAN arbeitet. Daher besteht grundsätzlich in Häusern mit vielen verschiedenen Drahtlosnetzwerken ein erhöhtes Risiko für Verbindungsabbrüche. Sollte es zu häufigen Aussetzern kommen, kann der Sendekanal der EasyRC-Plattform geändert werden.
Die EasyRC-Plattform nutzt Batterien mit Systemspannungen von maximal ca. 12 V Gleichspannung. Diese Spannung ist ungefährlich für den Menschen; es kann zu keinen gefährlichen Stromschlägen kommen. Zudem ist die Platine des Fahrzeugs über eine Sicherung vor zu großem Stromfluss geschützt. Jedoch können Batterien bei unsachgemäßem Gebrauch (z.B. durch Überladen, Kurzschluss, mechanische Beschädigung) beschädigt werden, was zur Entzündung und zum Freisetzen gesundheitsschädlicher Inhaltsstoe führen kann. Die im Modellsystem verwendeten Lithium-Ionen-Batterien dürfen deshalb nur mit dafür geeigneten Ladegeräten aufgeladen werden. Die maximale Spannung (Ladeschlussspannung) einer einzelnen Zelle beträgt 4.2 V. Diese Spannung darf nicht überschritten werden! Die Batterien dürfen nicht weiterverwendet werden, wenn sie mechanisch beschädigt sind oder überladen worden sind. Ein Kurzschluss muss unbedingt vermieden werden. Auch eine Tiefentladung (<2.5 V) kann die Zellen irreparabel beschädigen. Die Platinen der Fernsteuerung und des Fahrzeugs sind verpolungsgeschützt. Da das Fahrzeug mit drei in Serie geschalteten Batteriezellen betrieben wird, muss beim Einsetzen der Batterien dennoch unbedingt auf die richtige Ausrichtung (Polarität) geachtet werden, um Schäden an den Batterien zu vermeiden. Batterien und Elektronikkomponenten dürfen nicht im Restmüll entsorgt werden, sondern müssen entsprechend der örtlichen Möglichkeiten umweltgerecht entsorgt bzw. recycelt werden.

5

### 1.2 Spezifikationen der EasyRC-Plattform

### 1.2.1 Fernsteuerung

Abmessungen: 80x40x41 mm³ (LxBxH)
Gewicht: ca. 125 g (inklusive Batterie)
Microcontroller: ESP32-C3
Drahtloskommunikation: 2,4 GHz (ESP-NOW Protokoll) Joystick: Alps 10k (Playstation 4 Modell) Stromversorgung: 1x 18650 Li-Ion Batterie (3,7 V) Energieverbrauch: ca. 0,5 W
Hinweise:
- Batterieanschluss verpolungsgeschützt
- Warnung bei niedriger Batteriespannung (<3,4 V): LED beginnt zu blinken
- Selbstkalibrierender Joystick

### 1.2.2 Fahrzeug

Abmessungen: 282x125x95 mm³ (LxBxH) Maßstab: 1:16
Gewicht: ca. 1 kg (inklusive Batterien)
Microcontroller: ESP32-C3
Drahtloskommunikation: 2,4 GHz (ESP-NOW Protokoll)
Motortreiber: Pololu DRV8876 (QFN)
Antriebsmotor: JGA25-370 Bürstenmotor mit Getriebe (12 V, 1000 U/min) Geschwindigkeit: max. 10 km/h
Lenkungsservo: MG90S Microservo mit Metallgetriebe Stromversorgung: 3x 18650 Li-Ion Batterie (11.1 V)
Stromverbrauch: ca. 0,8 W (Leerlauf); ca. 3-6 W (Fahrbetrieb)
Hinweise:
- Batterieanschluss verpolungsgeschützt
- Warnung bei niedriger Batteriespannung (<10,2 V): Motor deaktiviert, Buzzer piept
- Warnung bei fehlender Verbindung zur Fernsteuerung (>1 s): Motor deaktiviert, Buzzer piept
- Warnung bei ausbleibenden Nutzereingaben (kein Input für >1 min): Buzzer piept
- Selbstrückstellende Sicherung bei zu großem Stromfluss (>1.5 A)

6

## 2. Teilelisten

### 2.1 Elektronikbauteile

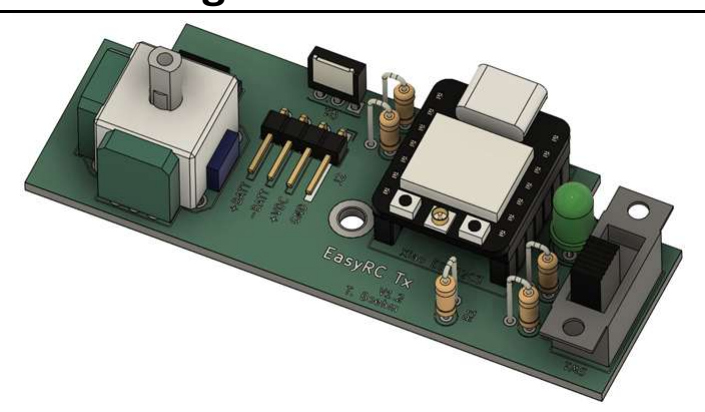
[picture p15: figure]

Abbildung | Bezeichnung | Beschreibung
| 1x EasyRC Tx Platine | Leiterplatte mit Komponenten für die Fernsteuerung. Beinhaltet den Joystick sowie den Microcontroller, der die Drahtlosverbindung herstellt. Komponentenliste in Kapitel 3.4.
| 1x EasyRC Rx Platine | Leiterplatte mit Komponenten für das Auto. Beinhaltet den Microcontroller für die Fahrzeugsteuerung und den Motortreiber für den Antriebsmotor. Komponentenliste in Kapitel 3.4.
| 1x RC-Servomotor, Typ MG90S, mit Servohorn Farbkodierung des Anschlusskabels: Gelb: Datenkanal Rot: +5 V Braun: GND | Motor mit integriertem Getriebe und Elektronik, der den Winkel der Motorachse in einem Winkelumfang von ca. 180° entsprechend seinem Eingangssignal ausrichtet. Das Servohorn dient als Verbindung zum bewegten Element und wird mit der Motorachse verschraubt. Wichtig: Auf richtige Anschlussrichtung achten. Verpolung zerstört den Servomotor!
| 1x DC-Getriebemotor JGA25-370 (1000 U/min) Das Anschlusskabel kann farbkodiert werden: Rot: +12 V Schwarz: GND | Motor mit integriertem Getriebe mit 1:10 Übersetzung. Die Drehzahl bei 12 V beträgt 1.000 U/min. Zur stabilen Kraftübertragung ist die Motorwelle in D-Form ausgeführt. Die Drehrichtung des Motors hängt von der Anschlussorientierung ab.

7

8x bedrahtete 5-mm-LED Das Anschlusskabel sollte farbkodiert werden: Rot: +5 V* (langer Pin) Schwarz: GND (kurzer Pin) *Gilt nur für EasyRC: Die benötigten Vorwiderstände für die LEDs sind auf der EasyRC-Platine integriert. | Leuchtdiode in verschiedenen Farben (2x Weiß, 4x Gelb und 2x Rot). Typ: Quadrios 2111O182 (weiß) Quadrios 2111O171 (gelb) Quadrios 2111O172 (rot) Wichtig: Beim Verlöten mit Litzen ausreichend lange Kabel (30-40 cm) verwenden und auf die Anschlussrichtung achten – die LED leuchtet nicht, wenn sie falsch angeschlossen ist und kann dadurch beschädigt werden!
4x 18650 Li Ion Batterie Spannungsfenster: 4.2 V (vollgeladen) 3.3 V (leer) | Typ: Lishen LR 1865SS 3.1 Ah Lithium-Ionen-Batterie für den Betrieb der EasyRC-Plattform. Die Batterien müssen über ein separat erhältliches Ladegerät aufgeladen werden. EasyRC prüft die Batteriespannung und warnt den Nutzer, wenn die Batterieladung zur Neige geht.
Batteriehalter für Einzelzellen Benötigte Größen: 1x 3 18650 Zellen 1x 1 18650 Zelle | Typ: mit Kabeln ausgestattete Halter Wichtig: Vor dem Einsetzen der Batterien immer auf die richtige Polarität achten! Die Batterien und die angeschlossenen Komponenten können bei Verpolung beschädigt werden.
1x An/Aus-Schalter | Typ: Marquardt 01801.1148-02 Schaltet das Fahrzeugmodell an und ab.

8

### 2.2 Metallbauteile

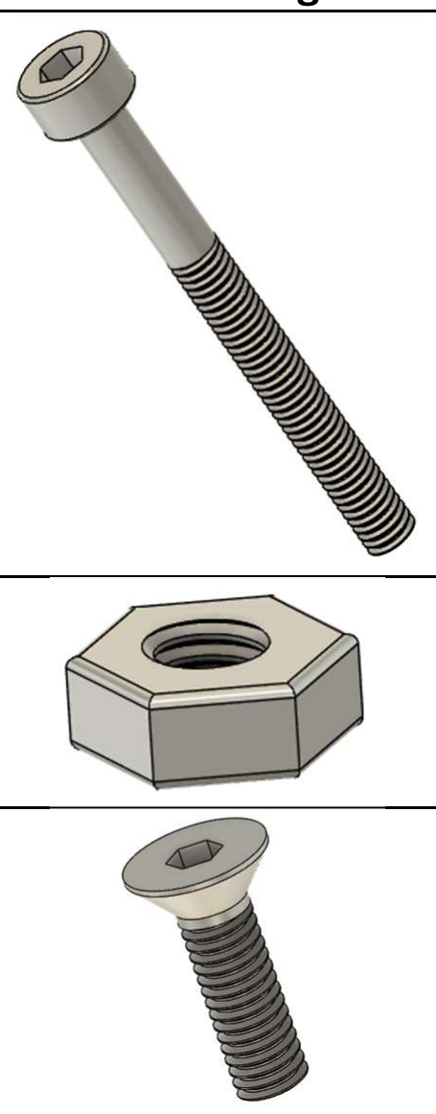
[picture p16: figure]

Abbildung | Bezeichnung | Beschreibung
| Zylinderkopfschraube M3 Benötigte Größen: 29x M3x8 mm 11x M3x16 mm 8x M3x20 mm 21x M3x30 mm | Schraube mit metrischem Gewinde mit 3 mm Durchmesser. Der Schraubenkopf wird mit einem 2,5 mm Innensechskantschlüssel angetrieben.
| 64x Sechskantmutter M3 | Mutter für Schrauben mit metrischem 3-mm-Gewinde.
| Senkkopfschraube M3 Benötigte Größe: 3x M3x10 mm | Schraube mit metrischem Gewinde mit 3 mm Durchmesser. Der Schraubenkopf wird mit einem 2,0 mm Innensechskantschlüssel angetrieben.
| Schraube M2.5 Benötigte Größe: 1x M2.5x6 mm | Schraube mit metrischem Gewinde mit 2,5 mm Durchmesser. Wird für die Befestigung des Servohorns benötigt.
| Rillenkugellager Benötigte Typen: 4x 605 (5x14x5 mm) 4x 608 (8x22x7 mm) 2x 6802 (15x24x5 mm) | Die Größenbezeichnungen der Lager geben Innendurchmesser x Außendurchmesser x Höhe an.

9

### 2.3 Gedruckte Bauteile

Richtungsangaben bei den Drucktipps beziehen sich immer auf die Ausrichtung des Bauteils im gesamten Modell, nicht auf die Ausrichtung in den Bildern in der linken Spalte!

Abbildung | Bezeichnung, Kapitel | Drucktipps
| 1x Fernbedienung, unterer Zwischenrahmen Kapitel 4.1.1 | Oberseite auf Druckbett; Support empfohlen.

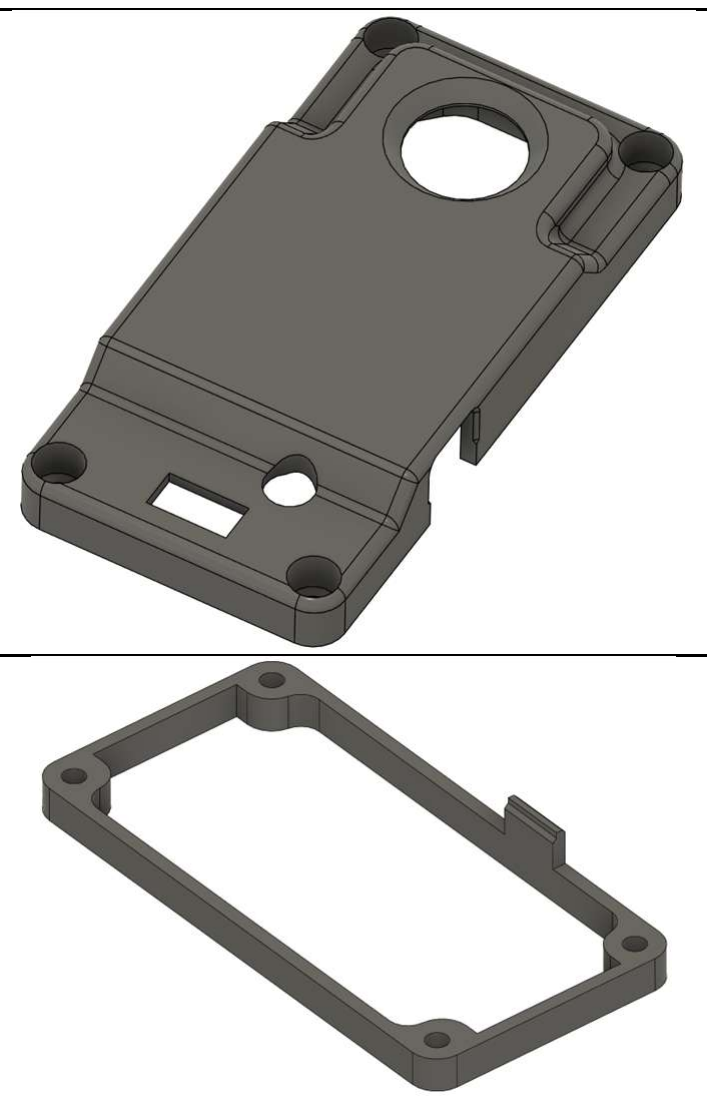
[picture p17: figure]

| 1x Fernbedienung, Deckel Kapitel 4.1.2 | Unterseite auf Druckbett; Support notwendig (organischer Support empfohlen).
| 1x Fernbedienung, oberer Zwischenrahmen Kapitel 4.1.2 | Unterseite auf Druckbett; kein Support notwendig.
| 1x Fernbedienung, Boden Kapitel 4.1.2 | Oberseite auf Druckbett; kein Support notwendig.

10

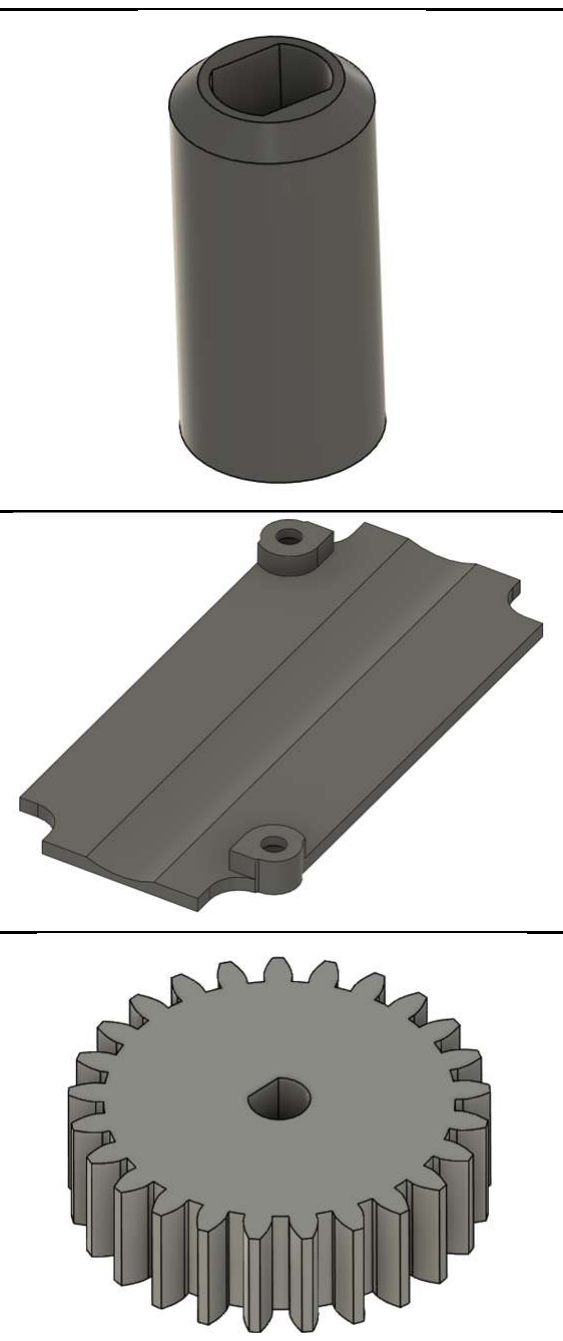
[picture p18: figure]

1x Fernbedienung, Joystick-Verlängerung Kapitel 4.1.3 | Oberseite auf Druckbett; kein Support notwendig
1x Fernbedienung, Batterieabdeckung Kapitel 4.1.3 | Unterseite auf Druckbett; kein Support notwendig
1x Motorritzel (25 Zähne) Kapitel 4.2.1 | Flache Seite auf Druckbett; kein Support notwendig. Bauteil am besten allein drucken!
1x Zwischenzahnrad (16 Zähne) mit 2x Lageraufnahme. Kapitel 4.2.2 | Zahnrad mit flacher Seite auf Druckbett (Bauteil am besten allein drucken); Lageraufnahme mit Außenseite auf Druckbett. Kein Support notwendig.
1x Dierentialzahnrad (24 Zähne) mit Abstandshalter Kapitel 4.2.3 | Zahnrad mit flacher Seite auf Druckbett (Bauteil am besten allein drucken).

11

2x Kronenzahnrad (15 Zähne) Kapitel 4.2.3 | Zahnrad wird zweimal benötigt. Mit den Zähnen nach oben drucken. Support ist zwingend notwendig!
2x Kronenzahnrader (10 Zähne) mit 1x Abstandshalter Kapitel 4.2.3 | Zahnrad wird zweimal benötigt. Mit den Zähnen nach oben drucken. Kein Support notwendig.
2x Dierential-Körper Kapitel 4.2.3 | Dierential-Körper wird zweimal benötigt. Mit der Außenseite nach oben drucken. Support ist zwingend notwendig (organischer Support empfohlen).
2x Hinterradfelge mit Reifen und Spacer Kapitel 4.2.4 | Felge mit der Außenseite nach unten drucken; Support notwendig. Spacer mit der Innenseite nach unten drucken. Reifen aus möglichst weichem TPU drucken.

12

2x Hinterradachse (in zwei Ausführungen mit 2.5 mm Längenunterschied) Kapitel 4.2.4 | Achsen sollten aus TPU gedruckt werden (hartes TPU ist empfohlen). Achsen mit der abgeflachten Seite nach unten drucken. Kein Support notwendig.
1x Chassis-Boden Kapitel 4.2.5 | Unterseite nach unten; Support wird benötigt.
1x Chassis-Abdeckung Kapitel 4.2.5 | Oberseite nach unten; kein Support notwendig.
2x Vorderradfelge mit Reifen, Sicherungsring und Spacer Kapitel 4.3.1 | Felge mit der Außenseite nach unten drucken. Spacer mit der Außenseite nach unten drucken. Support für beide Teile notwendig. Reifen aus möglichst weichem TPU drucken.
2x Vorderradaufhängung (gespiegelte Ausführungen für Links und Rechts) mit Spacer und Lenkgestänge-Verbinder Kapitel 4.3.1, 4.3.2 | Vorderradaufhängung mit der Unterseite nach unten drucken. Lenkgestänge-Verbinder mit der Oberseite nach unten drucken. Spacer mit der Innenseite nach unten drucken. Kein Support notwendig.

13

1x Lenkungsbügel Kapitel 4.3.2 | Oberseite nach unten, kein Support notwendig.
1x Chassis-Sicherungsbügel Kapitel 4.3.3 | Oberseite nach unten, kein Support notwendig.
1x Batteriefach-Abdeckung Kapitel 4.4.2 | Unterseite nach unten, kein Support notwendig.
1x Hinterer Stoßfänger Kapitel 4.4.3 | Oberseite nach unten, kein Support notwendig.
1x Vorderer Stoßfänger Kapitel 4.4.3 | Unterseite nach unten, kein Support notwendig.

14

1x Servohorn-Aufsatz Kapitel 0 | Oberseite nach unten, kein Support notwendig. Aus TPU drucken! Der Servohorn-Aufsatz ist als keinere und größere Ausführung vorhanden. Die für das Servohorn passende Größe muss gedruckt werden (siehe 0).
1x Karosserie, Heck Kapitel 4.5.1 | Verbindungsseite zur Front nach unten. Organischer Support notwendig. Rand zur besseren Haftung aktivieren.
1x Heckspoiler-Halterung Kapitel 4.5.1 | Innenseite (zur Fahrzeugfront zeigende Seite) nach unten. Kein Support notwendig.
1x Heckspoiler Kapitel 4.5.1 | Rückseite nach unten. Support notwendig. Rand für bessere Haftung aktivieren.
1x Karosserie, Front Kapitel 4.5.2 | Verbindungsseite zum Heck nach unten. Organischer Support notwendig. Rand zur besseren Haftung aktivieren.

15

Scheiben (1x Front, 1x links vorn, 1x links hinten, 1x rechts vorn, 1x rechts hinten, 1x Heck) Kapitel 4.5.2 | Scheiben mit den Außenseiten nach unten drucken. Kein Support notwendig.
1x Scheibenhalterung Kapitel 4.5.2 | Oberseite nach unten, Support empfohlen.
1x Frontlichtverklemmung mit 2x LED-Einsatz Kapitel 4.5.3 | Frontlichtverklemmung mit der Oberseite nach unten drucken, Support ist notwendig. LED-Einsatz mit den Innenseiten (zur Verklemmung zeigend) nach unten drucken. LED-Einsatz wird zweimal benötigt.
2x Rücklichtverklemmung und Auspu mit LED-Einsatz (LED-Einsatz in gespiegelten Ausführungen für Links und Rechts) Kapitel 4.5.4 | Rücklichtverklemmung und LED-Einsatz mit der Innenseite (zur Fahrzeugfront zeigende Seite) nach unten drucken. Kein Support notwendig. Die Verklemmung wird zweimal benötigt.

16

## 3. Elektronik

### 3.1 Einführung in die Elektronik

EasyRC nutzt den ESP32 Microcontroller für die Fernsteuerung, um Nutzereingaben über den Joystick zu erfassen und diese drahtlos an das Fahrzeug zu senden. Im Fahrzeug befindet sich ebenfalls ein ESP32 Microcontroller, um diese Datenpakete zu empfangen und in Befehle für die Lenkung und den Antriebsmotor umzusetzen. Es wird eine kleine Entwicklerplatine, der Xiao ESP32-C3 der Firma SEEEDStudio genutzt, da diese Plattform alle benötigten Komponenten enthält, um den Microcontroller zu programmieren (via USB-C), die benötigte Stromversorgung für den Microcontroller (3.3 V) aus einer höheren Eingangsspannung bereitstellen kann und mit einfach erreichbaren Pins zur Verbindung mit Peripherie ausgestattet ist. Der ESP32 ist für ein solches System die ideale Wahl, da es sich hierbei um einen sehr kostengünstigen Microcontroller handelt, der alle benötigten Funktionen ohne externe Zusatzchips bereitstellt: Er verfügt nicht nur über digitale Ein- und Ausgänge (um einfache Schalter auszulesen bzw. An/Aus-Befehle auszugeben), sondern auch über analoge Eingänge, um Sensoren mit nicht-diskreten Messsignalen auszulesen und in digitale Informationen umzuwandeln. Dazu beinhaltet der ESP32 Analog-Digital-Wandler, die ein variables Messsignal wie den Joystick der Fernbedienung fein aufgelöst in verarbeitbare Zahlenwerte für den Microcontroller umwandeln. Für eine ebenso feine Ansteuerung des Lenkungsmotors und des Antriebsmotors verfügt der ESP32 über PWMtaugliche Ausgänge. PWM steht für Pulsweitenmodulation und ist eine Methode, um über einen digitalen Ausgang, der nur 1 oder 0 ausgeben kann, ein fein dierenziertes Signal zu übertragen, indem die zeitliche Komponente berücksichtigt wird (wie lange je Ausgabezyklus ist der Ausgang auf 1 bzw. auf 0 gesetzt? („PWM-Tastgrad“)). Dabei kann der ESP32 den Ausgabezyklus, auch PWM-Frequenz genannt, in einem sehr breiten Intervall anpassen sowie gleichzeitig unterschiedliche Frequenzen auf unterschiedlichen Ausgängen bereitstellen. Zu guter Letzt beinhaltet der ESP32 auch ein Modul zur drahtlosen Kommunikation. Er funkt bei 2,4 GHz und kann so mit herkömmlichen WiFi-Netzwerken kommunizieren. In diesem Fall wird davon allerdings kein Gebrauch gemacht, sondern das ESP-eigene 2,4-GHz-Kommunikationsprotokoll ESP-NOW genutzt. Damit kann unabhängig von (nicht) vorhandenen WLAN eine Verbindung zwischen zwei ESP32-Microcontrollern aufgebaut werden, sodass die Fernsteuerung ihre Datenpakete direkt zum Fahrzeug schicken kann. Die Xiao ESP32-C3 Entwicklerplatine kommt außerdem mit einer mitgelieferten externen Antenne. Sie muss installiert werden, um die erforderliche Funkreichweite für ein ferngesteuertes Fahrzeug zu erreichen.
Der ESP32 enthält somit alle grundsätzlichen Funktionen für den Einsatz als Funk- und Kontrolleinheit für die EasyRC-Plattform, aber es werden dennoch noch Leiterplatten benötigt, die weitere Komponenten enthalten, um das Fahrzeug und die Fernsteuerung verwenden zu können. So werden beispielsweise für die LED-Beleuchtung des Fahrzeugs Transistoren als Schalter verwendet, da die Leuchtdioden mehr Strom benötigen, als der Microcontroller direkt bereitstellen kann. Er schaltet über den Transistor eine separate Stromversorgung für die LEDs. Für den Antriebsmotor wird ein separater Motortreiber benötigt, der eine ähnliche Funktion wie der Transistor für die LEDs erfüllt, aber noch mehr können muss: Er erlaubt es, die Drehrichtung und Geschwindigkeit eines Gleichstrom-Bürstenmotors mithilfe von nur zwei Pins (einer gibt die Drehrichtung vor, der andere die Geschwindigkeit) einzustellen. Dazu kommen kleinere Ergänzungen wie Widerstände als Spannungsteiler, um den ESP32 die Batteriespannung auslesen zu lassen, oder ein aus einem Transistor aufgebauter Verpolungsschutz, der die Platinen davor schützt, bei falsch angeschlossener Batterie zerstört zu werden.

17

### 3.2 Fertigung und Bestückung der Leiterplatten

Die Fertigungsdateien für die Leiterplatten sind auf GitHub verfügbar (https://github.com/TRD-B/EasyRC), können bei verschiedenen Auftragsfertigern wie JLCPCB, PCBWay oder Aisler bestellt werden und anschließend mit den benötigten Komponenten bestückt werden. Dazu sollte bleifreies Lötzinn verwendet werden (Gesundheitsschutz!). Die zu verlötenden Komponenten sind vorwiegend SMD-Bauteile, also Komponenten, die lediglich auf die Oberseite der Platine gelegt und anschließend mit der Platine verlötet werden. Das ist etwas schwieriger als THT-Bauteile, die durch die Platine gesteckt und auf der Rückseite verlötet werden, da sie beim Lötvorgang noch nicht fixiert sind. Die SMD-Bauteile sind aber kleiner als vergleichbare THT-Bauteile, sodass die Platinen kompakter gehalten werden können. Außerdem kommen nur Größen zum Einsatz, die noch groß genug sind, um ohne Spezialwerkzeug mit einem Handlötkolben verlötet zu werden (kleinste Größe: 0805 (2 mm x 1,25 mm)).
Als Faustregel für das Bestücken von Leiterplatten gilt, dass mit den kleinsten SMD-Bauteilen begonnen werden sollte. So arbeitet man sich von klein nach groß und erst am Schluss werden THT-Bauteile verlötet. So wird verhindert, dass bereits platzierte Komponenten bei den folgenden Schritten im Weg sind. Für ein komfortables Arbeiten ist eine „helfende Hand“, also eine mit flexiblen Armen ausgestattete Halterung für die Leiterplatte empfehlenswert. Die SMD-Bauteile werden am einfachsten verlötet, indem sie mit einer feinen Pinzette gehalten und dann am ersten Kontaktpad verlötet werden. Sobald sie an einer Stelle fixiert sind, halten sie ohne Pinzette und können an den verbleibenden Stellen verlötet werden. Wichtig ist, beim weiteren Löten nicht den ersten Kontakt wieder zu schmelzen, da sie ansonsten verschoben werden. Die verwendeten SMD-Bauteile lassen sich leicht richtig auf den Platinen orientieren: Widerstände und Keramik-Kondensatoren besitzen nur zwei Kontakte und sind „unpolar“, setzen also keine bestimmte Einbaurichtung voraus. Die Transistoren besitzen drei Kontakte, können jedoch aufgrund ihrer Geometrie nicht falsch positioniert werden (wenn die drei Kontakte auf den Pads der Leiterplatte aufliegen, ist der Transistor richtig ausgerichtet). Bei den THT-Komponenten muss mehr auf die richtige Positionierung geachtet werden: Der Piezo-Buzzer ist auf einer Seite mit „+“ beschriftet und auch die Elektrolyt-Kondensatoren sind polarisierte Bauteile, müssen also mit der Anode (kurzer Pin) zum Pluspol und der Kathode (langer Pin; weißer breiter Streifen auf dem Gehäuse mit schwarzem „-“) zum Minuspol ausgerichtet werden. Dasselbe gilt für die LEDs, deren Anschlusspins ebenfalls polarisiert sind (Anode kurz; Kathode lang). Beim Verlöten der Stiftleisten, die zum Anschließen externer Bauteile benötigt werden, kann eine Buchsenleiste als Hilfe verwendet werden, um die Stiftleiste vertikal ausgerichtet zu halten. Alternativ kann dafür auch eine Pinzette verwendet werden. Als letztes sollten die großen Bauteile (Joystick-Modul der Fernsteuerung und Spannungswandler, Piezo-Buzzer sowie Elektrolytkondensatoren der Fahrzeugplatine) verlötet werden.
Nach dem Verlöten der Komponenten muss geprüft werden, dass sämtliche Kontakte korrekt hergestellt worden sind (jeder Kontakt muss mechanisch stabil verlötet sein: ein leichtes Drücken mit dem Finger gegen die Komponente darf diese nicht ablösen) und, dass keine Lötbrücken zwischen verschiedenen Kontakten vorhanden sind (Lötzinnverbindungen, die benachbarte Kontaktpads überbrücken). Erst wenn das nach optischer Prüfung gewährleistet worden ist, dürfen die Platinen mit den aufsteckbaren ESP32-C3 Leiterplatten sowie dem Pololu Motortreiber bestückt und mit Strom versorgt werden. Bei den aufsteckbaren Leiterplatten muss auf die richtige Ausrichtung geachtet werden, da sie andernfalls (bei Montage um 180° gedreht) nicht funktionieren und beschädigt werden können.

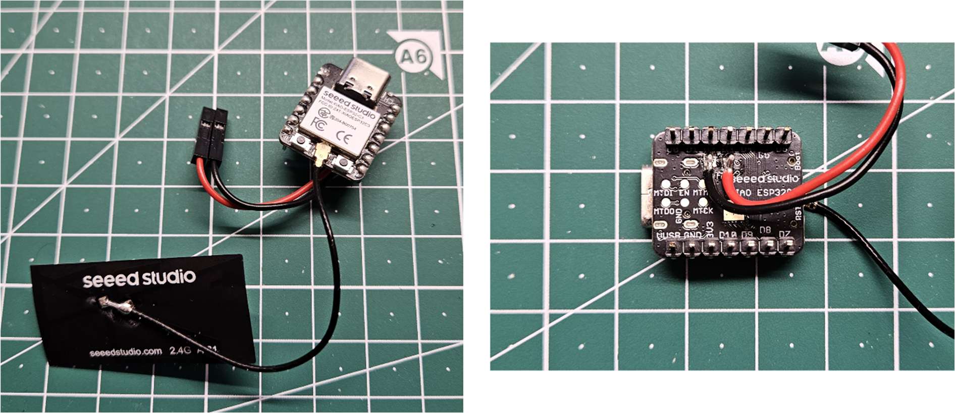
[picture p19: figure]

18

### 3.3 Crimpen und Verlöten der Elektronikbauteile

Zur Verbindung zwischen den Leiterplatten und den damit verbundenen Elektronikbauteilen (siehe Kapitel 2.1) sollten Kabel mit einem Querschnitt von 0.25 mm² verwendet werden. Das ist zwar mehr als für die LEDs notwendig ist, reicht aber für den Motor und den An/Aus-Schalter des Fahrzeugs aus und so muss nur mit einer Größe gearbeitet werden. Es empfiehlt sich, eine Kupferlitze mit roter und eine mit schwarzer Isolierung zu nutzen, um Bauteile mit Polarisierung (z.B. LEDs) ohne Probleme korrekt gepolt anschließen zu können: Als gängige Konvention wird Rot für Plus und Schwarz für Minus eingesetzt.
Die Elektronikbauteile werden bauteilseitig mit den Litzen verlötet und platinenseitig mit 2.54 mm Dupont-Steckern (weiblich, Buchse) gecrimpt, sodass sie einfach ein- und ausgesteckt werden können. Beim Crimpen sollte darauf geachtet werden, dass die Verbindung mechanisch stabil ist: Die Litze darf sich auch unter Zug nicht aus dem Crimp-Pin lösen. Je nach verwendetem Crimp-Werkzeug muss die Isolierung der Litze separat gecrimpt werden (Crimpen in zwei Schritten) oder wird in einem Arbeitsschritt mit vercrimpt. Bei letzterem kann es vorkommen, dass die Isolierung nicht mit ausreichend Druck gecrimpt wird, sodass noch mit einer Zange nachgecrimpt werden muss, um den Pin ohne Probleme in das Buchsengehäuse einführen zu können.
Die beiden folgenden Bilder zeigen den Xiao ESP32-C3 der Fernsteuerung. Die Antenne muss auch am Microcontroller des Fahrzeugs installiert werden, aber nur der Microcontroller für die Fernsteuerung benötigt verlötete Kabel an den Energieversorgungspads auf der Unterseite der Platine. Bei der Fernsteuerung sollte darauf geachtet werden, dass die Anschlussleitungen zwischen ESP32-C3 und Platine bzw. Batteriehalter und Platine so kurz ausgeführt werden, dass sich das Gehäuse problemlos schließen lässt (siehe auch Kapitel 4.1.1). Beim Fahrzeug sollte hingegen eher mit etwas längeren Leitungen gearbeitet werden, da hier ein Verstauen der Kabel einfacher möglich ist. Vor allem die LEDs des Fahrzeugs benötigen lange Anschlussleitungen (empfehlenswert sind 30-40 cm), um das Auf- und Absetzen der Karosserie ohne ein versehentliches Abstecken der LEDs zu ermöglichen. Der Motor und der An/Ausschalter des Fahrzeugs benötigen keine unterschiedlich farbkodierten Kabel, da die Anschlussrichtung beim Schalter keine Rolle spielt und die Drehrichtung des Motors, die von der Polarisierung abhängt, einfach im Code der Fernsteuerung korrigiert werden kann (Kapitel 5.2).

19

### 3.4 Komponentenliste

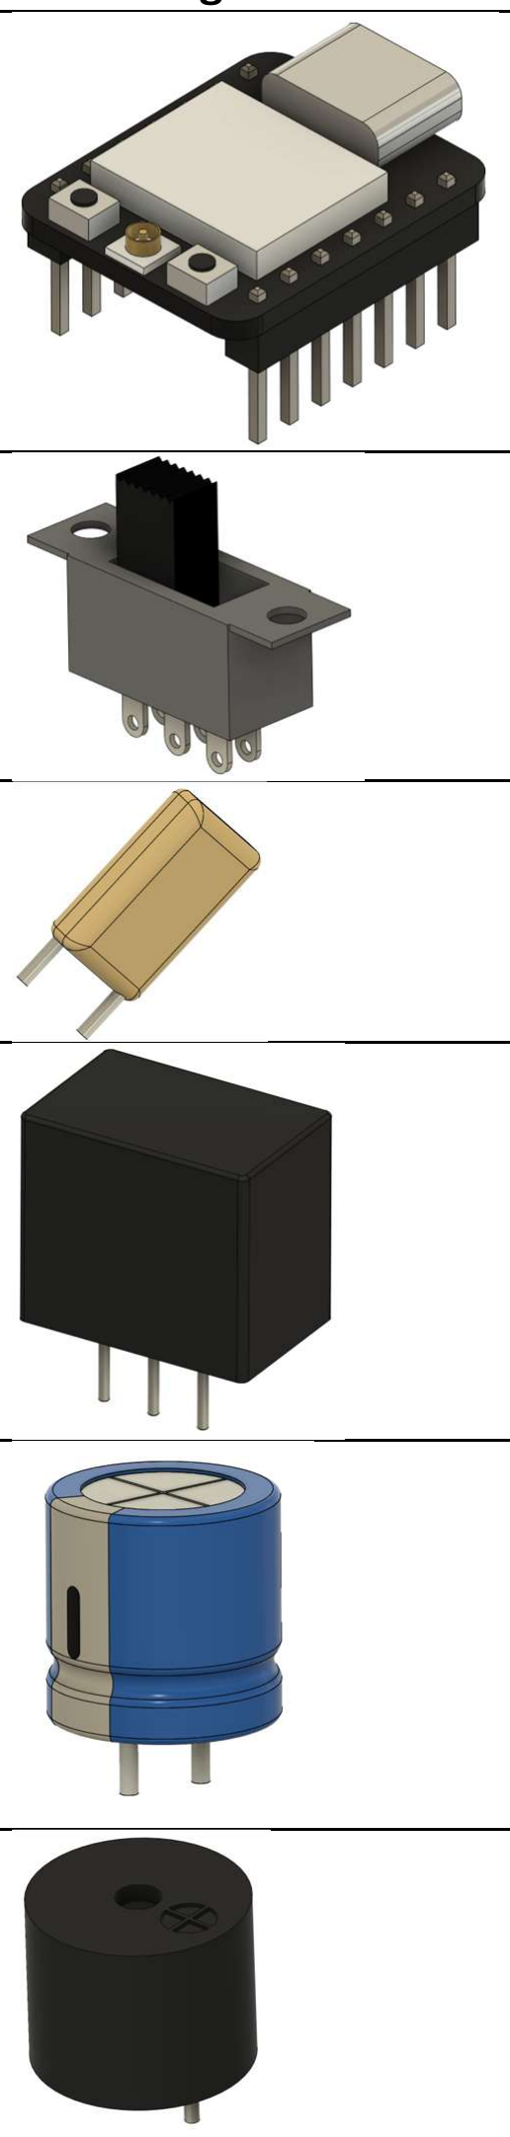
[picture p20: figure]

Abbildung | Bezeichnung | Beschreibung
| 2x Microcontroller-Entwicklerplatine | Typ: SEEED Studio Xiao ESP32-C3
| 1x Miniatur-Schiebeschalter | 6-Pol, Typ Wentronic S 166. Schieber-Höhe: 6-10 mm
| 1x Selbstrückstellende PTC-Sicherung, 3 A | Type: ESKA FRG300-16F
| 1x DC-DC Wandler, 5 V 1 A | 3-Pol Bauform, Pin-kompatibel mit LMxx-Linearreglern Typ: Traco TSR1-2450E
| Elektrolyt-Kondensator, 2x 25 V 100 µF 1x 25 V 22 µF | 100 µF: 6,3 mm Durchmesser, 2,5 mm Rastermaß (Typ: Panasonic EEUFM1E101) 22 µF: 5 mm Durchmesser, 2,5 mm Rastermaß (Typ: Panasonic EEAFC1E220H)
| 1x Piezo-Buzzer | 12 mm Durchmesser, 6,5 mm Rastermaß Typ: HITPOINT PB1220PE05Q
| 1x 5mm LED bedrahtet, grün | Typ: Quadrios 2111O169

20

1x Motortreiber Breakout-Board | Typ: Pololu DRV8876QFN
6x MOSFET n-Kanal, 17 A 55 V | Bauform: TO-251AA Typ: Infineon IRLU 024N
1x Zener-Diode, 8,2 V | Bauform: DO-41 (DO-204AL) Typ: SEMTECH BZX85C8V2 R0
1x Schottky-Diode, 20 V 1 A | Bauform: DO-41 Typ: Taiwan Semiconductor 1N 5817
Widerstand, 0,6 W Benötigte Widerstandswerte: 1x 330 Ohm 16x 470 Ohm 4x 1 kOhm 1x 10 kOhm 3x 22 kOhm 2x 33 kOhm 2x 100 kOhm | Bauform: THT 0207 Typ: Yageo MF0207FTE52
Joystick-Modul (kompatibel mit PS4-Controller) | Typ: ALPS 10kOhm
Stiftleiste, 2,54 mm Rastermaß Benötigte Größen: 1x 1x4 (gewinkelt) 4x 1x2 (gerade) 1x 1x3 (gerade) 4x 2x4 (gerade) | Typ: W+P 946-14-004-00 (1x4 gewinkelt) MPE 087-1-002-0-S-XS0-1260 (1x20, kann gekürzt werden) MPE 087-2-040-0-S-XS0-1260 (2x20, kann gekürzt werden)

21

Buchsenleiste, 2,54 mm
Rastermaß.
Benötigte Größen:
4x 1x7 (8.5 mm Höhe)
2x 1x7 (5 mm Höhe)

Typ: MPE 094-1-007-0-NFX-YS0 (8.5 mm Höhe)
Frei BL 1X10G 2,54 (5 mm
Höhe, muss auf 1x7 gekürzt werden)

Für die Fernbedienung
werden niedrigere Leisten
benötigt, um die Bauhöhe der Platine kleiner zu halten. Dazu müssen die Stifte der Microcontroller-Platine
gekürzt werden.

22

### 3.5 Übersicht Fernsteuerungselektronik

### 3.5.1 Schaltplan

Netzbezeichnungen:
+BATT: Batterie-Anode (1S LiIon)
+VDC: Batterie-Anode nach An/Aus-Schalter
+3V3: Geregelte 3.3 V (DC-DC Wandler in Xiao ESP32-C3 integriert) -BATT: Batterie-Kathode
GND: Batterie-Kathode nach Verpolungsschutz

23

Erläuterungen zu den Ausschnitten des Schaltplans:
- Microcontroller: Umfasst die Ein- und Ausgänge des Xiao ESP32-C3. An Pin D0 wird die Batteriespannung über einen Spannungsteiler halbiert, um sicher mittels des analogen Eingangs des Microcontrollers gemessen werden zu können. Die Pins D1 bis D3 werden mit dem Joystick-Modul verbunden. Da als Analogpins die Pins D0 bis D2 verwendet werden können, sind D1 und D2 für die beiden Achsen des Joysticks vorgesehen. D3 wird als digitaler Eingang für den Druckknopf des Joystick-Moduls genutzt. Die LED an Pin D7 wird mit einem Vorwiderstand betrieben, um zu verhindern, dass die LED durchbrennt oder der Microcontroller durch zu viel Stromabgabe beschädigt wird (der Stromfluss sollte nicht mehr als 10-15 mA betragen). Der Funktionsumfang der Pins kann hier nachgelesen werden:
https://wiki.seeedstudio.com/XIAO_ESP32C3_Getting_Started/#
- Connectors: Hier werden die verschiedenen Ein- und Ausgänge der Platine abgebildet. Der Miniaturschalter verfügt über zwei galvanisch getrennte Schalter, von denen nur einer benötigt wird, um die Stromzufuhr zur Platine an- und abzuschalten. Der 4-Pin-Anschluss wird dazu genutzt, um die Platine mit der Batterie sowie mit den Stromversorgungspads auf der Unterseite des Xiao ESP32-C3 zu verbinden. Die Stromversorgungspins des Xiao ESP32-C3 erlauben es, den Microcontroller direkt mit einer einzelnen LiIon-Batterie zu betreiben, da die Entwicklerplatine über einen integrierten Spannungswandler verfügt, der aus der Batteriespannung stabile 3.3 V erzeugt.
- Reverse polarity protection: Als Verpolungsschutz für die Platine wird ein „falschherum“ verbauter n-Kanal MOSFET zwischen der Batterie-Kathode und der Platine verwendet. Das sorgt dafür, dass die Platine bei korrekt gepolter Batteriespannung über die Bodydiode des Transistors mit Strom versorgt werden kann. Sobald das erfolgt, liegt auch am Gate eine positive Spannung an, sodass der Transistor durchschaltet und der Spannungsabfall über die Bodydiode des Transistors als Verlust wegfällt. Sollte die Batterie verpolt angeschlossen werden, sperrt die Bodydiode des Transistors den Stromfluss und am Gate liegt eine negative Spannung an (+VDC entspricht der negativen Batteriespannung), sodass kein Strom zwischen Source und Drain fließen kann. Der Transistor verhält sich als ideale Diode.
- Joystick module: Die beiden Potentiometer des Joysticks werden mit 3.3 V aus dem ESP32-C3 gespeist, sodass die Analogausgänge eine für den Microcontroller messbare Spannung zwischen Logiklevel (3.3 V) und gemeinsamer Masse (0 V) bereitstellen. Der Druckknopf wird mit Masse und dem Microcontroller verbunden, sodass dieser mithilfe eines internen Pullup-Widerstands die Zustände 0 und 1 einnehmen kann (je nachdem, ob der Knopf gedrückt wird oder nicht).

24

### 3.5.2 Leiterplatte

Bezeichnung | Komponente
D1 | 5 mm LED, grün
J1 | Alps 10k Joystick-Modul
J2 | 1x4 2,54 mm gewinkelte Stiftleiste
Q1 | TO-251AA MOSFET IRLU 024N
R1 | 0207 Widerstand 33 kOhm
R2 | 0207 Widerstand 33 kOhm
R3 | 0207 Widerstand 10 kOhm
R4 | 0207 Widerstand 100 kOhm
R5 | 0207 Widerstand 330 Ohm
SW2 | Wentronic S 166 6-Pol Miniaturschalter
U1 | 2x 1x7 2,54 mm Buchsenleiste (5 mm Bauhöhe)
Anmerkung: Auf die Revision der Leiterplatte achten!

Ein Foto der mit Microcontroller bestückten und mit der Batteriehalterung verbundenen Platine ist in Kapitel 4.1.1 abgebildet.

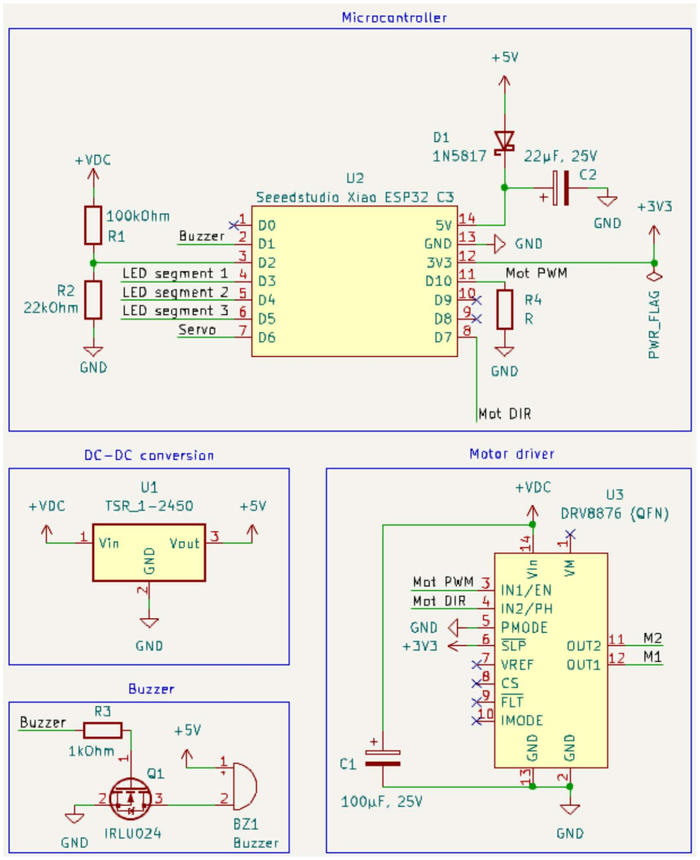
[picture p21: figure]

25

### 3.6 Übersicht Fahrzeugelektronik

### 3.6.1 Schaltplan

26

Netzbezeichnungen:
+BATT: Batterie-Anode (3S LiIon)
+VDC: Batterie-Anode nach An/Aus-Schalter
+5V: Geregelte 5V (DC-DC Wandler)
+3V3: Geregelte 3.3 V (DC-DC Wandler in Xiao ESP32-C3 integriert) -BATT: Batterie-Kathode
GND: Batterie-Kathode nach Verpolungsschutz

27

Erläuterungen zu den Ausschnitten des Schaltplans:
- Microcontroller: Umfasst die Ein- und Ausgänge des Xiao ESP32-C3. An Pin D2 wird die Batteriespannung über einen Spannungsteiler reduziert, um sicher mittels des analogen Eingangs des Microcontrollers gemessen werden zu können. Die Pins D1, D3 bis D7 und D10 dienen als Ausgänge. D1, D6 und D10 werden als PWM-Ausgänge verwendet; die anderen als einfache digitale Ausgänge. An D10 (PWM-Steuerung des Antriebsmotors) wird Widerstand R4 hinzugefügt, der als optionaler Pulldown-Widerstand dient. Wenn hier ein hochohmiger Widerstand eingesetzt wird, können unkontrollierte Motorbewegungen beim Hochfahren des Microcontrollers, wenn der Ausgang D10 noch undefiniert ist (floated), verhindert werden. Der 5 V-Eingang des Microcontrollers wird mit einer Schottky-Diode geschützt. So wird verhindert, dass bei einer bestehenden USB-Verbindung Strom vom PC zur Platine fließen kann, da dies den USB-Ausgang überlasten könnte. Am 5 V-Eingang des Microcontrollers wird ein Kondensator verbaut, um Spannungsschwankungen zu minimieren und einen stabilen Betrieb zu gewährleisten.
- DC-DC conversion: Hier wird der Abwärtswandler gezeigt, der aus der 3S LiIon-Batterieversorgung der Platine stabile 5 V für den Microcontroller, den Servomotor der Lenkung, die LEDs und den Piezo-Buzzer erzeugt.
- Motor driver: Der Pololu-Motortreiber wird über zwei Pins des Microcontrollers mit Daten versorgt (Geschwindigkeit und Drehrichtung). Die weiteren Pins des Treibers werden fix mit Logikspannung und Masse verbunden oder bleiben unverbunden. In der Nähe des Motortreibers wird ein Stützkondensator verbaut, um bei schnellen Laständerungen des Antriebsmotors eine stabile Spannung aufrechtzuerhalten. Der Motor wird an die Ausgänge M1 und M2 des Motortreibers angeschlossen. Informationen zur Pinbelegung und Steuerung des Motortreibers können hier nachgelesen werden: https://www.pololu.com/product/4037
- Buzzer: Der Piezo-Buzzer erzeugt Geräusche mit bestimmten Frequenzen, wenn eine wechselnde Spannung anliegt. Dazu wird ein PWM-Ausgang des Microcontrollers verwendet, sodass die am Piezo-Buzzer anliegende Spannung zwischen 0 V und 5 V wechselt, wobei die Frequenz über die PWM-Frequenz des Microcontrollers vorgegeben wird und damit die Tonhöhe des Piezo-Buzzers vorgibt. Da der Buzzer mehr Strom benötigt, als der Microcontroller bereitstellen kann und für den Betrieb mit 5 V statt den 3,3 V des Microcontrollers ausgelegt ist, wird ein Transistor als Schalter eingesetzt, der über den PWM-Ausgang des Microcontrollers an- und abgeschaltet wird.
- LED connectors: Die LED-Anschlüsse auf der Platine sind in vier Gruppen mit je vier Anschlussmöglichkeiten unterteilt. LED-Segment 0 kann nicht vom Microcontroller gesteuert werden, sondern erhält permanent Strom. Dieses Segment ist für die Frontscheinwerfer vorgesehen. Die Segmente 1 bis 3 werden (wie auch der Piezo-Buzzer) von einem über einen Transistor geschalteten Ausgang des Microcontrollers gesteuert und dienen deshalb als Blinker und Bremslicht. Jeder LED-Ausgang enthält einen eigenen Vorwiderstand, um den Stromfluss je LED zu begrenzen. Hierfür sind 470 Ohm vorgesehen, wobei dieser Wert auch angepasst werden kann, um die Lichtintensität einzustellen (bitte nicht den zulässigen Maximalstrom der LED überschreiten und die maximale thermische Verlustleistung der Vorwiderstände beachten!).
- Connectors: Hier sind die Platinenanschlüsse sowie der Verpolungsschutz der Platine dargestellt. Die positive Batterieverbindung wird vom Batterieanschluss an den An-/Ausschalter weitergegeben, der dann wiederum die Platine mit Energie versorgt. Dabei wird eine Sicherung verbaut, die im Falle eines zu großen Stromflusses auslöst. Zudem

28

wird dasselbe Verpolungsschutz-Konzept wie auch bei der Fernsteuerungsplatine genutzt. Hier wird ein Spannungsteiler eingesetzt, da der Transistor für eine maximale Gatespannung von 16 V ausgelegt ist und die Platine bei vollgeladenen Batterien 12,6 V erhält, also recht nahe an diesem Grenzwert liegt. Der Spannungsteiler halbiert diese Spannung, um in einem sicheren Bereich für den Transistor zu bleiben. Zudem wird eine Zener-Diode als zusätzliche Sicherung verwendet, um im Falle von induktiven Spannungsspitzen den Transistor zu schützen. In der Nähe des Servomotor-Anschlusses wird ein Stützkondensator verbaut, um Spannungseinbrüche bei Laständerungen des Lenkungsmotors zu minimieren.

29

### 3.6.2 Leiterplatte

30

Bezeichnung | Komponente
BATT | 1x2 2,54 mm Stiftleiste
BZ1 | Piezo-Buzzer (12 mm, 6,5 mm Rastermaß)
C1 | Elektrolytkondensator, 6,3 mm, 2,5 mm Rastermaß, 100 µF, 25 V
C2 | Elektrolytkondensator, 5 mm, 2,5 mm Rastermaß, 22 µF, 25 V
C3 | Elektrolytkondensator, 6,3 mm, 2,5 mm Rastermaß, 100 µF, 25 V
D1 | DO-41 Schottky-Diode 20 V 1 A
D2 | DO-41 Zener-Diode 8,2 V
F1 | PTC-Sicherung 3 A (ESKA FRG300-16F)
LEDs 0 | 2x4 2,54 mm Stiftleiste mit 4x 0207 Widerstand 470 Ohm
LEDs 1 | 2x4 2,54 mm Stiftleiste mit 4x 0207 Widerstand 470 Ohm
LEDs 2 | 2x4 2,54 mm Stiftleiste mit 4x 0207 Widerstand 470 Ohm
LEDs 3 | 2x4 2,54 mm Stiftleiste mit 4x 0207 Widerstand 470 Ohm
Motor | 1x2 2,54 mm Stiftleiste
PWR SW | 1x2 2,54 mm Stiftleiste
Q1 | TO-251AA MOSFET IRLU 024N
Q2 | TO-251AA MOSFET IRLU 024N
Q3 | TO-251AA MOSFET IRLU 024N
Q4 | TO-251AA MOSFET IRLU 024N
Q5 | TO-251AA MOSFET IRLU 024N
R1 | 0207 Widerstand 100 kOhm
R2 | 0207 Widerstand 22 kOhm
R3 | 0207 Widerstand 1 kOhm
R4 | (optional) 0207 Widerstand 10-100 kOhm
R5 | 0207 Widerstand 1 kOhm
R6 | 0207 Widerstand 1 kOhm
R7 | 0207 Widerstand 1 kOhm
R24 | 0207 Widerstand 22 kOhm
R25 | 0207 Widerstand 22 kOhm
Servo | 1x3 2,54 mm Stiftleiste
U1 | DC-DC Wandler Traco TSR1-2450E
U2 | 2x 1x7 2,54 mm Buchsenleiste (8,5 mm Bauhöhe)
U3 | 2x 1x7 2,54 mm Buchsenleiste (8,5 mm Bauhöhe)
Anmerkung: Auf die Revision der Leiterplatte achten! Aus Platzgründen sind die Widerstände R8 bis R23 (LED-Vorwiderstände) auf der Platine nicht beschriftet.

Die Übersicht der Anschlüsse ist in Kapitel 4.4.4 zu finden. Wichtig beim Aufsetzen des Xiao ESP32-C3 und des Motortreibers ist die richtige Ausrichtung: Für den Microcontroller ist die Ausrichtung des USB-Anschlusses auf der Leiterplatte angezeichnet und für den Motortreiber sind die Positionen der beiden Pins VM und VIn auf der Leiterplatte gekennzeichnet. Falschausrichtung kann diese Komponenten zerstören!

31

## 4. Bauanleitung Fernsteuerung und Fahrzeug

Für den Zusammenbau des Modellfahrzeugs und der Fernsteuerung werden die Komponenten aus den Teilelisten benötigt. Als Werkzeuge werden Innensechskantschlüssel in den Größen 2 und 2,5 mm mit Kugelkopf benötigt. Zudem werden eine kleine flache Zange und eine Pinzette benötigt bzw. sind hilfreich.
Als Material für den 3D-Druck der Bauteile wird PETG empfohlen, da dieser Kunststo leicht zu drucken ist, eine ausreichende mechanische Stabilität bietet und UV-beständig ist. Alternativ kann allerdings auch PLA oder ein anderes gängiges Filament für mechanisch stabile, steife Drucke eingesetzt werden. Einige Bauteile müssen aus flexiblem TPU gedruckt werden. Diese sind in Kapitel 2.3 entsprechend gekennzeichnet und tragen „TPU“ im Namen. Für den Druck aller Bauteile ist ein Druckbett mit wenigstens 220 mm Länge notwendig. Empfehlungen für die Orientierung der Bauteile auf dem Druckbett sowie zum Support sind in den Hinweisen zu den gedruckten Bauteilen gelistet. Für alle Bauteile gilt, dass diese am besten mit einer 0,4 mm Düse sowie mit einer Schichthöhe von 0,2 mm gedruckt werden sollten. Eine Infill-Rate von 15 % ist ausreichend.
Zu den gedruckten Bauteilen muss angemerkt werden, dass diese keine perfekte Passform aufweisen. Das ergibt sich aus der Fertigung: 3D-Druck erzeugt in bestimmten Ausrichtungen keine perfekten Toleranzen (z.B. werden in Z-Richtung beim Drucken mit einer Schichthöhe von 0,2 mm Schritte in dieser Höhe ausgeführt, sodass sich die Form des Bauteils, sofern keine horizontale oder vertikale Kante vorliegt, der gewünschten Form nur annähern kann). Zudem benötigt 3D-Druck für bestimmte Geometrien Stützstrukturen, die die Form während des Drucks stabilisieren (man kann nicht in Luft drucken, sondern benötigt Kontakt zur Bodenplatte des Druckers, um eine Form stabil herstellen zu können). Diese Stützstrukturen, die auch Support genannt werden, verkleben teilweise mit den Bauteilen und sorgen deshalb für unsaubere Oberflächen. Die gedruckten Bauteile müssen vollständig von Support-Rückständen befreit werden, um eine korrekte Passung zu gewährleisten.
Teilweise kommt es auch zu Artefakten beim 3D-Druck, wie Stringing (es verbleiben dünne Kunststofäden zwischen oder innerhalb von Bauteilen) oder Verzerrungen der Geometrie („Elefantenfuß“ oder Warping: Das Bauteil verzieht sich unmittelbar über der Bodenplatte des Druckers durch die auftretenden Temperatur- und Luftbewegungsschwankungen während des Druckprozesses). Die EasyRC-Komponenten wurden so entwickelt, dass diese Eekte möglichst vollständig vermieden oder aber in ihrer Auswirkung auf die Funktion vernachlässigbar sind. Dennoch kann es vorkommen, dass Bauteile nicht perfekt in ihre Position passen, rotierende Elemente in ihrem Gehäuse schleifen, oder Aussparungen für Schrauben und Muttern zu eng ausfallen, um Verschraubungen einfach durchführen zu können.
Deshalb ist es wichtig, beim Zusammenbau auf diese möglichen Fehler zu achten: Bevor Bauteile verschraubt werden, sollte geprüft werden, ob sich Schrauben einfach in die vorgesehenen Kanäle schieben lassen. Falls das nur schwer geht, sollte der Kanal ggf. mit einer längeren Schraube vorbearbeitet werden, indem das Schraubengewinde als Feile genutzt wird und durch Auf- und Abbewegungen überschüssiger Kunststo abgetragen wird. Bei rotierenden Elementen sollte vor dem Verschrauben immer die Leichtgängigkeit geprüft werden. Fällt ein Schleifgeräusch auf, sollte geprüft werden, ob irgendwo ein Kunststofaden oder eine Oberflächenungenauigkeit vorliegt, der oder die die Reibung erzeugt. Überschüssiges Material sollte vorsichtig mit einem Schlitzschraubendreher oder Schleifpapier entfernt werden. Der Vorteil 3D-gedruckter Bauteile

32

ist ihr geringer Preis und ihre schnelle Fertigung (bei kleinen Stückzahlen): Sollte ein Bauteil defekt sein, kann es innerhalb weniger Stunden neu gefertigt werden, sodass ein rascher Austausch beschädigter Komponenten möglich ist.
Das EasyRC-Modell wird mithilfe von metrischen Schrauben und Muttern zusammengesetzt. Es werden Muttern als Gewindeeinsätze verwendet, da kleine gedruckte Gewinde nur eine sehr geringe Stabilität aufweisen und deshalb nur wenige Male verwendet werden können, bevor sie abgerieben/abgetragen worden sind. Alternativ könnten gedruckte Bauteile auch mit Cyanacrylat-Kleber (Sekundenkleber) verbunden werden, was allerdings kein Lösen der Bauteile ohne ihre Zerstörung ermöglicht. Sekundenkleber oder Heißkleber können aber als schnelle Reparaturmöglichkeit für gebrochene Bauteile genutzt werden.
Bei den Schraubverbindungen ist es wichtig, die Muttern vor dem Verbinden der Komponenten korrekt in ihre jeweiligen Vertiefungen zu setzen. Das ist rein von Hand teilweise schwierig, was sowohl von der Position der Mutter in einem Bauteil als auch von den Toleranzen der Bauteile abhängt. Um das Einsetzen der Muttern zu vereinfachen, kann man diese auf eine Schraube drehen und mithilfe der Schraube im korrekten Winkel in die Vertiefung drücken. Alternativ setzt man die Mutter lose in die Vertiefung und greift sie von der gegenüberliegenden Seite mit einer Schraube, um sie in ihre Vertiefung zu ziehen. Diese beiden Möglichkeiten sind in der folgenden Abbildung dargestellt.

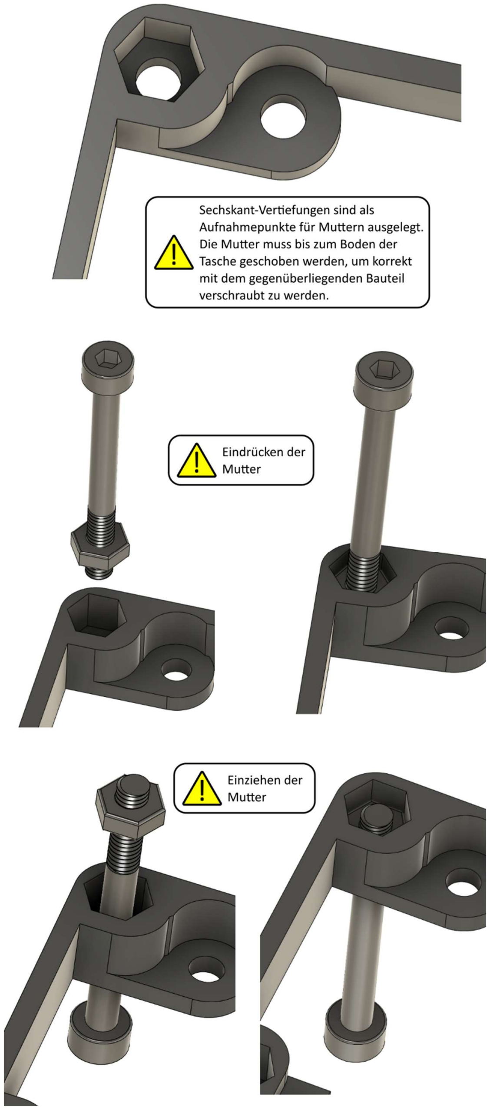
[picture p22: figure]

33

34

Als Hilfestellung zum Finden der richtigen Schraubenlängen gibt es hier eine Größenliste. Wenn die Seite auf exaktem A4-Format ausgedruckt wird, entsprechen die gezeigten Größen genau den verschiedenen Schraubenlängen:

35

### 4.1 Fernbedienung

### 4.1.1 Einbau Leiterplatte und Batteriehalterung

Benötigte Bauteile: Fernbedienung Zwischenrahmen unten, EasyRC Tx Leiterplatte, Batteriehalterung 1x 18650 LiIon Zelle, M3x10 mm Senkkopfschraube, M3 Mutter

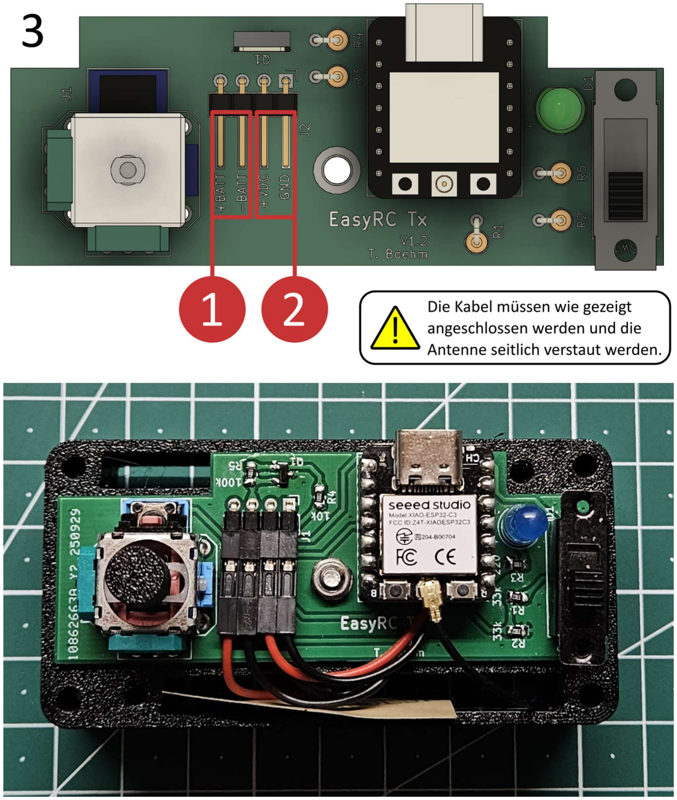
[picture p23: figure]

36

Anschlüsse: Die Batteriehalterung muss an (1) angeschlossen werden; das rote Kabel muss mit +BATT verbunden werden und das schwarze Kabel mit -BATT. Die Kabel vom Microcontroller müssen mit (2) verbunden werden; das rote Kabel wird an +VDC angeschlossen und das schwarze Kabel an GND.
Achtung: Der Batterieanschluss (1) ist verpolungsgeschützt, der Microcontroller aber nicht! Sollte (2) falschherum angeschlossen werden, wird der Microcontroller unmittelbar zerstört, sobald die Fernsteuerung angeschaltet wird!

37

### 4.1.2 Befestigung Deckel und Boden

Benötigte Bauteile: Fernbedienung (vorbereitet), Fernbedienung Deckel, Fernbedienung Zwischenrahmen oben, Fernbedienung Boden, M3x30 mm Schraube (4x), M3 Mutter (6x)

38

39

### 4.1.3 Abschluss Fernbedienung

Benötigte Bauteile: Fernbedienung (vorbereitet), Fernbedienung Joystick-Verlängerung, Fernbedienung Batterieabdeckung, M3x8 mm Schraube (2x)

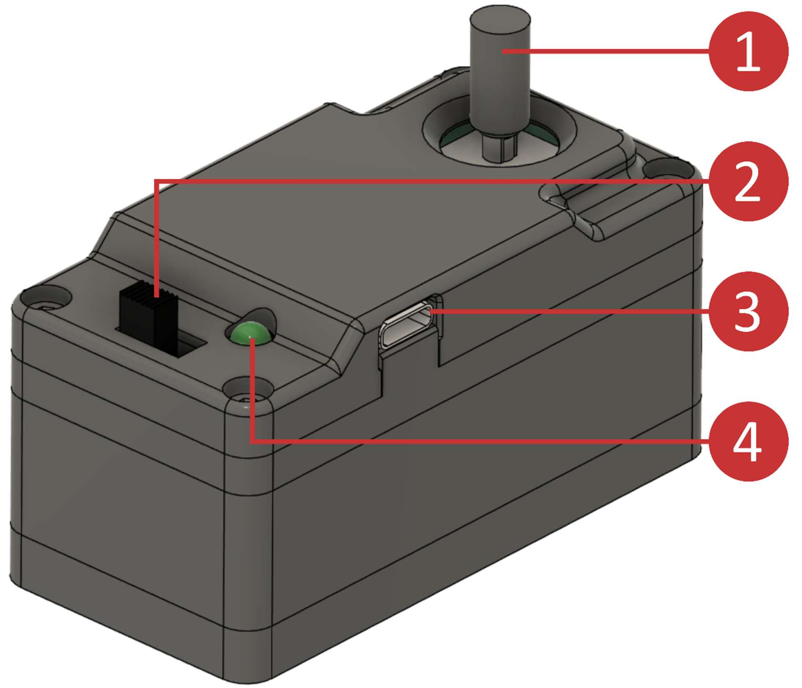
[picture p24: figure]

40

### 4.1.4 Übersicht Fernbedienung

Zahl | Bezeichnung | Erklärung
1 | Joystick | Joystick zur Steuerung des Fahrzeugs (vorwärts/rückwärts/links/rechts). Drücken des Joysticks löst die Hupe des Fahrzeugs aus.
2 | An/Aus-Schieber | Position links: aus; Position rechts: an
3 | USB-Anschluss | USB-Anschluss Typ C
4 | Status-LED | Leuchtet durchgehend, wenn die Fernbedienung angeschaltet ist. Blinkt 2x pro Sekunde, wenn die Batterie schwach ist.

41

### 4.2 Antriebsstrang und Hinterräder

### 4.2.1 Vorbereitung Motor

Benötigte Bauteile: DC-Getriebemotor, Motorritzel

42

### 4.2.2 Zwischenzahnrad

Benötigte Bauteile: Zwischenzahnrad mit Lageraufnahme (2x), Kugellager 605 (5x14x5 mm, 2x), M3x30 mm Schraube, M3 Mutter

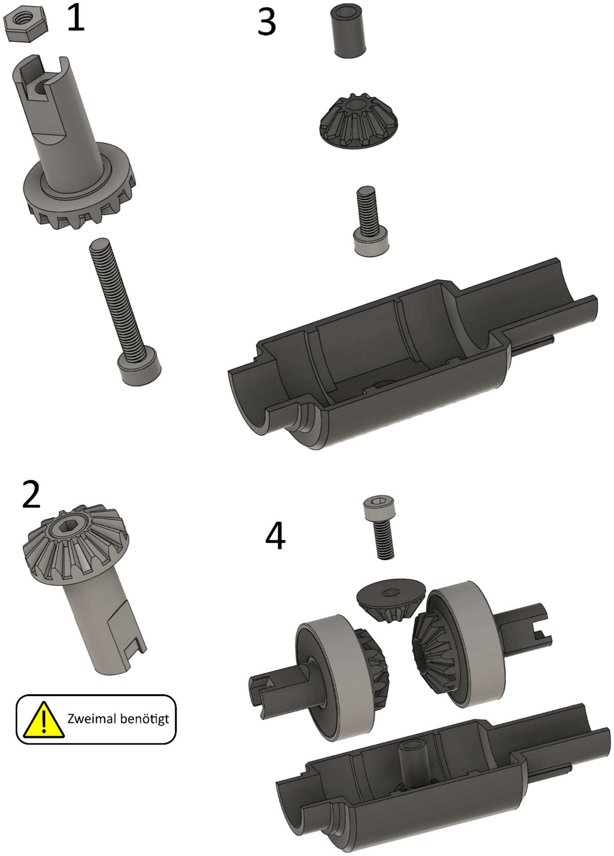
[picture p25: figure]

43

### 4.2.3 Dierential

Benötigte Bauteile: Dierential-Körper (2x), Kronenzahnräder (10 Zähne) mit Abstandshalter (2x), Kronenzahnrad (15 Zähne, 2x), Dierentialzahnrad (24 Zähne) mit Abstandshalter (2x), Kugellager 608 (8x22x7 mm, 2x), Kugellager 6802 (15x24x5 mm, 2x), M3x8 mm Schraube (2x), M3x20 mm Schraube (2x), M3 Mutter (2x)

44

45

### Schon gewusst?

Ein Dierential ist in jedem Auto verbaut. Ein Dierential wird benötigt, um bei einer angetriebenen Achse unterschiedlich schnelle Drehzahlen der Räder zu ermöglichen. Das ist für Kurvenfahrten wichtig: In einer Kurve muss das innere Rad langsamer als das äußere Rad drehen können, damit die Haftung nicht verloren geht. Fahrzeuge mit Hinter- oder Vorderradantrieb benötigen je nur ein Dierential zwischen dem linken und rechten angetriebenen Rad. Autos mit Allradantrieb benötigen sogar drei Dierentiale (vorn und hinten zwischen den linken und rechten Rädern, sowie ein Mitteldierential zwischen der vorderen und hinteren Achse).
Der Nachteil eines Dierentials wird deutlich, wenn ein Rad die Bodenhaftung verliert. Dann dreht dieses Rad frei, während das andere Rad stillsteht – das Auto steckt fest. Für Straßenfahrzeuge spielt das keine Rolle, da dieser Fall quasi nie auftritt. Für Geländefahrzeuge ist das hingegen ein häufiges Problem. Dafür gibt es Spezialdierentiale, die selbstsperrend wirken, oder manuell zu betätigende Dierentialsperren: Die Dierentialfunktion wird mechanisch ausgehebelt, sodass beide angetriebenen Räder gleich schnell drehen müssen. Die Dierentialsperre darf aber nur im Gelände aktiviert werden, da im normalen Straßenverkehr zusätzlicher Reifenabrieb, schlechtere Kurvenhaftung und eine unnötig starke Beanspruchung des Antriebsstrangs auftreten.

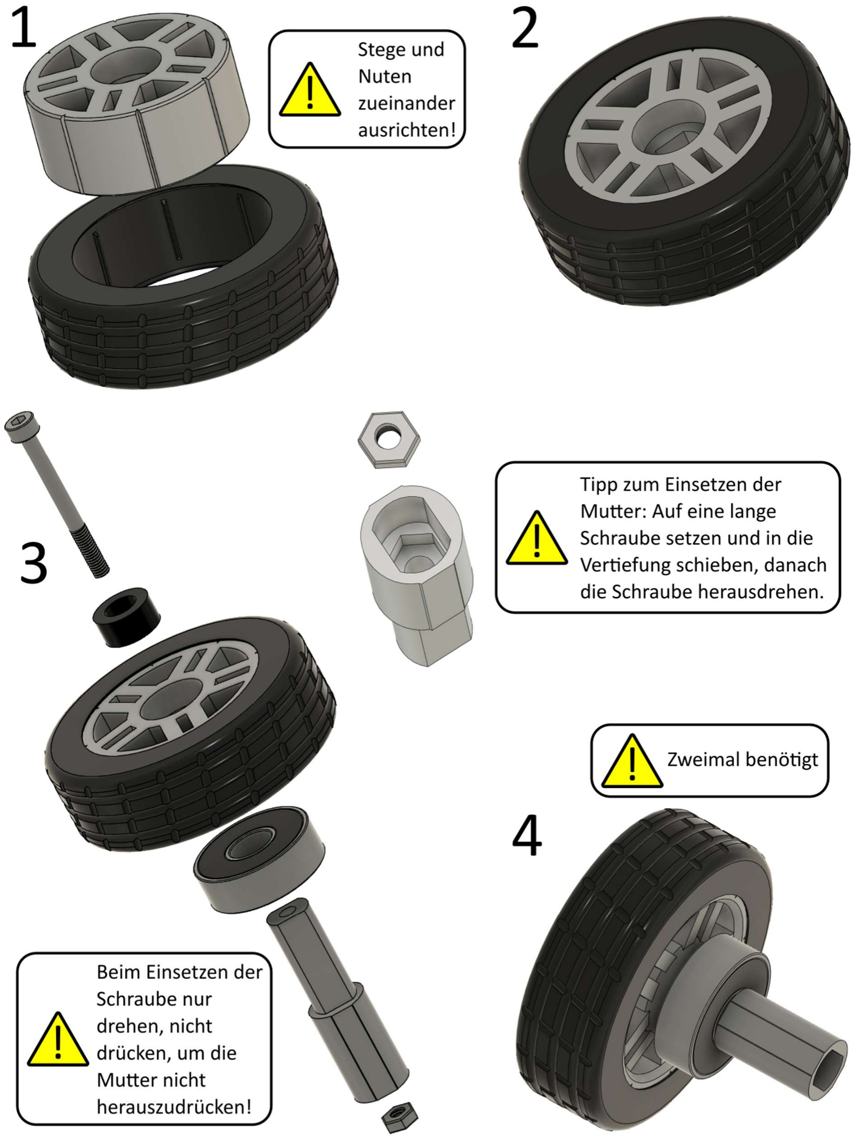
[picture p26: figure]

46

### 4.2.4 Hinterräder

Benötigte Bauteile: Hinterradfelge (2x), Reifen (2x), Spacer Hinterradfelge (2x), Linke Hinterradachse, Rechte Hinterradachse, Kugellager 608 (8x22x7 mm, 2x), M3x30 mm Schraube (2x), M3 Mutter (2x)

47

### 4.2.5 Verbindung Antriebsstrang und Chassis

Benötigte Bauteile: Hinterräder, Dierential, Zwischenzahnrad, Motor mit Ritzel (alle bereits vorbereitet), Chassis-Boden, Chassis Deckel, M3x30 mm Schraube (8x), M3 Mutter (14x)

48

49

50

### Schon gewusst?

Getriebe sind allgegenwärtig: Nicht nur im Auto, sondern auch in jeder Bohrmaschine, in mechanischen Uhren oder sogar in Salatschleudern sind Getriebe enthalten. Ein Getriebe sorgt dafür, dass die Drehzahl eines mechanischen Antriebs erhöht oder reduziert wird. Im Gegenzug wird das Drehmoment (die Kraft) kleiner oder größer, da sich die Leistung eines mechanischen Antriebs aus Drehmoment x Drehzahl ergibt. Ein ideales Getriebe hat kaum Reibungsverluste, sodass der Wirkungsgrad meist bei >90% liegt. Das heißt, dass der Abtrieb eines Motors mit einer 1:10 Übersetzung zwar zehnmal langsamer dreht, aber dafür auch fast zehnmal so stark ist. Die Übersetzung ergibt sich aus dem Verhältnis der Zähnezahl des Zahnradpaars.
Im EasyRC-Modell ist ein Getriebe bereits im Motor integriert, weil die gewünschte 1:10-Übersetzung mit gedruckten Bauteilen nur über ein mehrstufiges Getriebe erreicht werden kann, was viel Platz kosten würde und die Fehleranfälligkeit erhöhen würde. Das gedruckte Getriebe im EasyRC-Modell (25:24-Übersetzung, also annähernd 1:1) dient nur dazu, den Motor weit genug von der Antriebsachse zu entfernen, um Platz für das Dierential zu schaen. Die Anzahl der Zähne des Zwischenzahnrads spielt dabei keine Rolle: Entscheidend für die Getriebeübersetzung sind lediglich die Zahnräder der Antriebs- und Abtriebswelle.

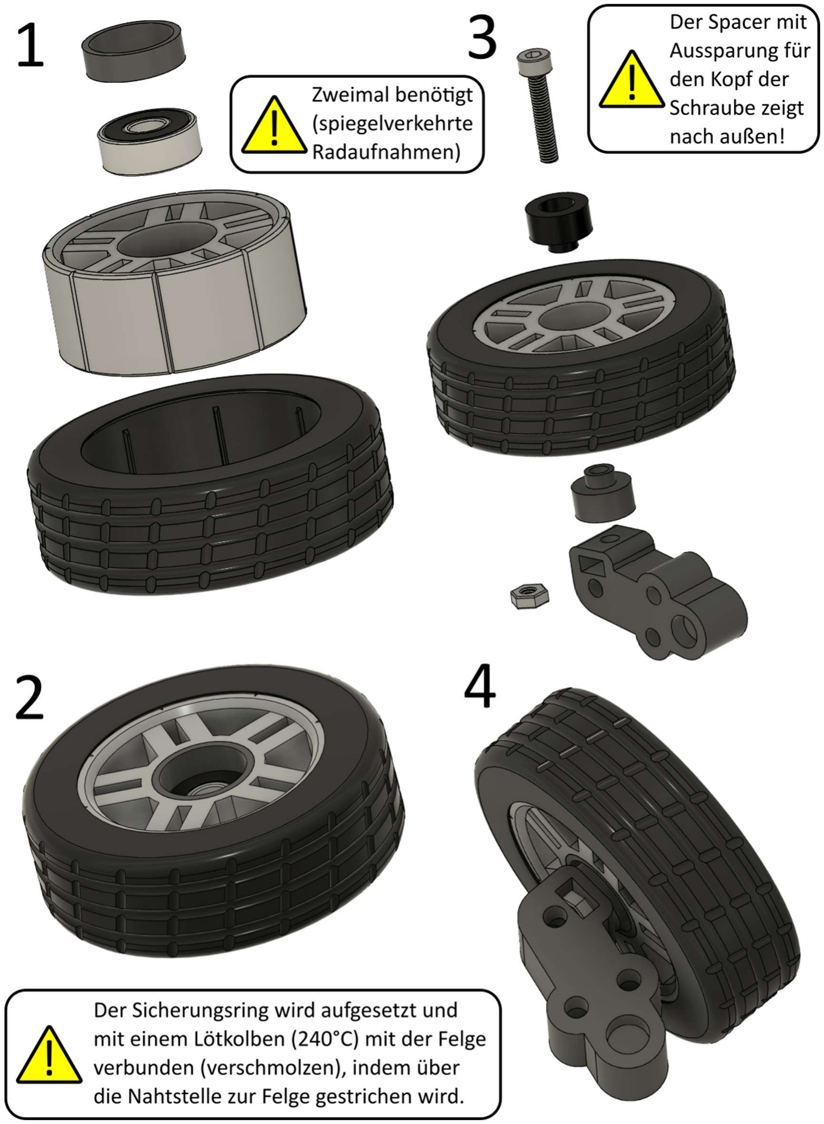
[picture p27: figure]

51

### 4.3 Vorderräder und Lenkung

### 4.3.1 Vorbereitung Vorderräder

Benötigte Bauteile: Vorderradfelge (2x), Reifen (2x), Vorderrad-Sicherungsring (2x), Vorderrad-Spacer (2x), Vorderradaufhängung (2x, gespiegelte Versionen), Vorderradaufhängung-Spacer (2x), Kugellager 605 (5x14x5 mm, 2x), M3x16 mm Schraube (2x), M3 Mutter (2x)

52

### 4.3.2 Lenkgestänge

Benötigte Bauteile: Vorbereitete Vorderräder, Lenkungsbügel, Lenkgestänge-Verbinder (2x), M3x16 mm Schraube (2x), M3x20 mm Schraube (4x), M3 Mutter (4x)

53

### 4.3.3 Verbindung von Vorderrädern und Chassis

Benötigte Bauteile: Vorbereitetes Chassis, Vorbereitete Vorderräder mit Lenkgestänge, Chassis-Sicherungsbügel, MG90S Servomotor, M3x20 mm Schraube (2x), M3x30 mm Schraube (2x), M3 Mutter (4x)

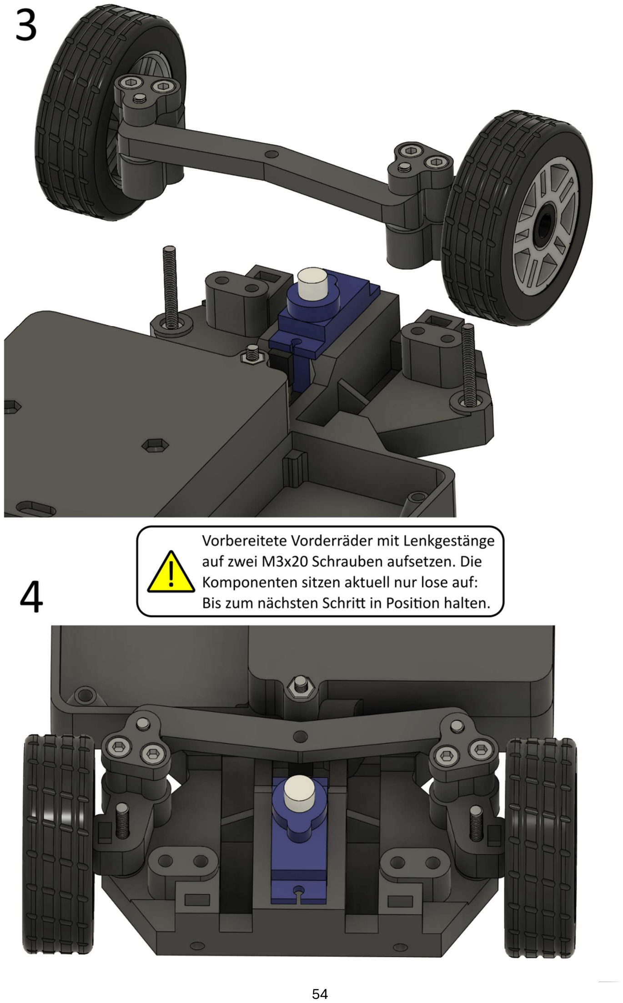
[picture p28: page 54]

54

55

56

### Schon gewusst?

Wenn das Lenkrad in einer Kurve eingeschlagen wird, dann bewegt sich das innere Rad weiter als das äußere: Der Lenkungswinkel des inneren Rades ist größer als der des äußeren Rades. Diese Anordnung wird Ackermann-Lenkgeometrie genannt und unterstützt die Haftung des Fahrzeugs in engen Kurven. Da in einem Auto nur die Vorderräder gelenkt werden, muss es in einer Kurve auf einem Kreis fahren, dessen Mittelpunkt eine Verlängerung der Hinterachse ist, damit die Räder nicht anfangen zu rutschen. Das ist auch der Grund, wieso man in engen Parklücken besser rückwärts als vorwärts einparken kann: Der Wendepunkt befindet sich immer auf der Höhe der Hinterachse.
Werden die Vorderräder in dieser Konstellation mit dem exakt gleichen Winkel eingeschlagen, treen sich ihre Winkel nicht in diesem Mittelpunkt. In der Konsequenz können sie nicht auf einer stabilen Kreisbahn rollen, sondern müssen entgegen ihrer Laufrichtung gezogen werden. Die Ackermann-Lenkgeometrie nähert beide Vorderräder dem idealen Kurvenmittelpunkt an, sodass das Auto in der Kurve so stabil wie möglich fahren kann. Dieses Konzept wurde für Pferdekutschen entwickelt und in Autos übernommen. Allerdings nutzen Autos oftmals keine vollständige Ackermann-Lenkgeometrie, da dieses Konzept vor allem bei langsamem Fahren die Stabilität erhöht. Schnelle Kurvenfahrten sorgen für verschiedene weitere Eekte, wie eine Verlagerung der Fahrzeugmasse auf die kurvenäußeren Räder und die Neigung des Fahrzeugs zur Kurvenaußenseite, was dafür sorgt, dass andere Lenkgeometrien besser funktionieren.
Den Extremfall stellen F1-Autos dar: Sie nutzen sogar anti-Ackermann-Lenkgeometrie, also stärker eingeschlagene kurvenäußere als kurveninnere Räder, um die Reifentemperatur durch zusätzliche Reibung (höheren Schräglaufwinkel) des kurveninneren Rades hochzuhalten. Denn im Hochgeschwindigkeitsbereich ist eine hohe Reifentemperatur notwendig, um beste Traktion zu gewährleisten. Die Nachteile dabei sind ein höherer Reifenabrieb und schlechtere Kurveneigenschaften bei langsamen Fahrten, was für diese Rennfahrzeuge allerdings keine Rolle spielt.

57

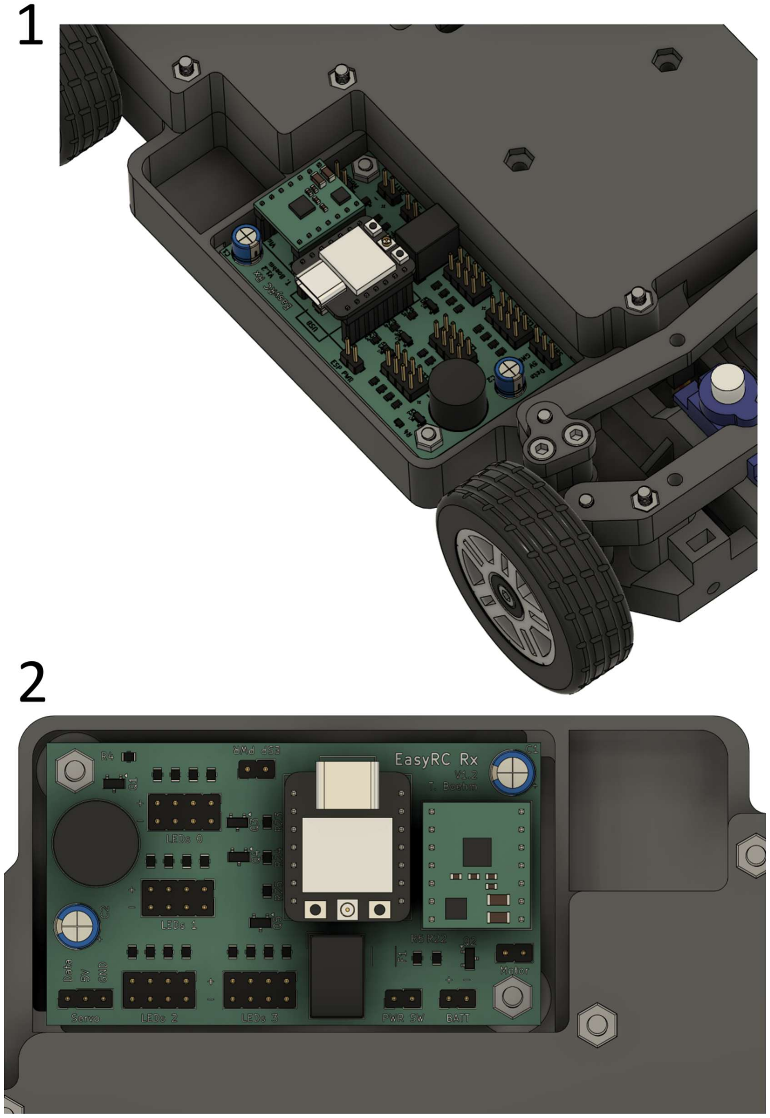
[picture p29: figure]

58

### 4.4 Finalisierung Chassis

### 4.4.1 Leiterplatte

Benötigte Bauteile: Vorbereitetes Chassis, EasyRC Rx-Platine, M3x16 mm Schraube (2x), M3 Mutter (2x)

59

### 4.4.2 Batteriefach

Benötigte Bauteile: Vorbereitetes Chassis, Batteriefach-Abdeckung, Batteriehalter 3x 18650 LiIon-Zelle, M3x16 mm Schraube (2x), M3x10 mm Senkkopfschraube (2x), M3 Mutter (2x)

60

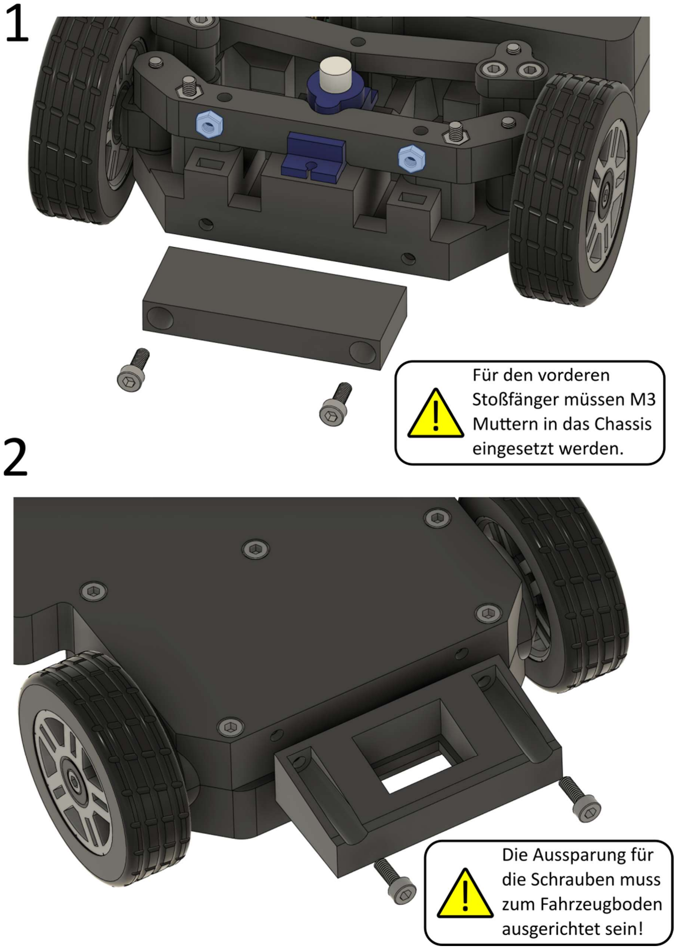
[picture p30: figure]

61

### 4.4.3 Stoßfänger

Benötigte Bauteile: Vorbereitetes Chassis, Vorderer Stoßfänger, Hinterer Stoßfänger, An/Aus-Schalter, M3x8 mm Schraube (4x), M3 Mutter (2x)

62

63

### 4.4.4 Verkabelung

Die Verkabelung des Chassis beinhaltet die Markierungen 1 bis 4: Batteriefach, An/Aus-Schalter, Antriebsmotor und Lenkung können bereits verkabelt werden. Unbedingt auf korrekte Polarität achten (siehe Tabelle)!
Die LEDs (Markierungen 5 bis 8) werden in Kapitel 5 beim finalen Zusammenbau des Fahrzeugs angeschlossen. Es können bis zu vier LEDs je Kanal angeschlossen werden. Die Standard-Karosserie ist für zwei LEDs je Kanal ausgelegt. Eine LED kann mit einem beliebigen Anschluss eines Kanals verbunden werden (ohne bevorzugte Reihenfolge).
Zahl | Bezeichnung | Polarität
1 | BATT (Batterieanschluss) | Rot zu +; Schwarz zu -
2 | PWR SW (An/Aus-Schalter) | Egal
3 | Motor (Antriebsmotor) | Egal (Drehrichtung wird per Software eingestellt)
4 | Servo (Lenkungsmotor) | Gelb zu Data; Rot zu 5V; Braun zu GND
5 | LEDs 0 (Frontscheinwerfer)* | Rot zu +; Schwarz zu -
6 | LEDs 1 (Bremslichter)* | Rot zu +; Schwarz zu -
7 | LEDs 2 (Blinker links)* | Rot zu +; Schwarz zu -
8 | LEDs 3 (Blinker rechts)* | Rot zu +; Schwarz zu -
*Die LED-Anschlussleisten bestehen aus vier Anschlusspaaren: Es können bis zu vier LEDs je Kanal angeschlossen werden. In dieser Ansicht sind die oberen Kontakte + und die unteren Kontakte -. Die Karosserie ist für zwei LEDs je Kanal ausgelegt.

64

### 4.4.5 Vorbereitung Servohorn

Benötigte Bauteile: Servohorn-Aufsatz, Servohorn, M3x16 mm Schraube, M3 Mutter

Für den Servohorn-Aufsatz existieren zwei 3D-Modelle, da es die Servohörner der MG90-Servos in verschiedenen Größen gibt. Das kleinere Servohorn hat eine Länge von ca. 32 mm und das größere eine Länge von ca. 37 mm. Es muss der Servohorn-Aufsatz mit der passenden Servohorn-Aussparung gedruckt und eingesetzt werden, um eine spielfreie Lenkung zu ermöglichen.

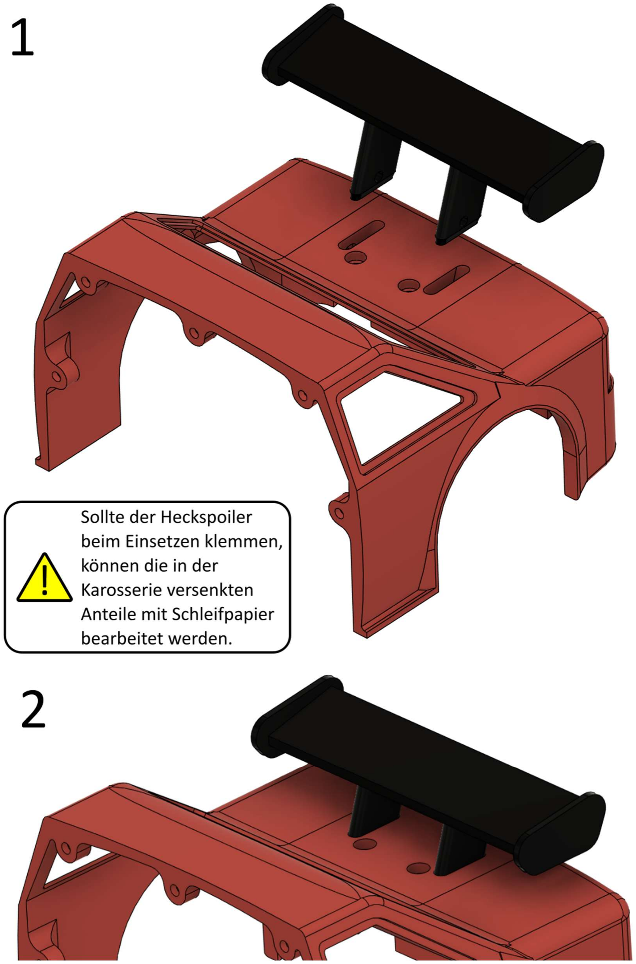
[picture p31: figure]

65

### 4.5 Karosserie

### 4.5.1 Heckspoiler

Benötigte Bauteile: Karosserie, Heck, Heckspoiler, Heckspoiler-Halterung, M3x8 mm Schraube (2x), M3x16 mm Schraube (2x), M3 Mutter (2x)

66

67

### 4.5.2 Karosserie-Verbindung und Scheiben

Benötigte Bauteile: Karosserie-Heck (vorbereitet), Karosserie-Front, Scheiben (1x Front, 1x links vorn, 1x links hinten, 1x rechts vorn, 1x rechts hinten, 1x Heck), Scheibenhalterung, M3x8 mm Schraube (15x), M3 Mutter (15x)

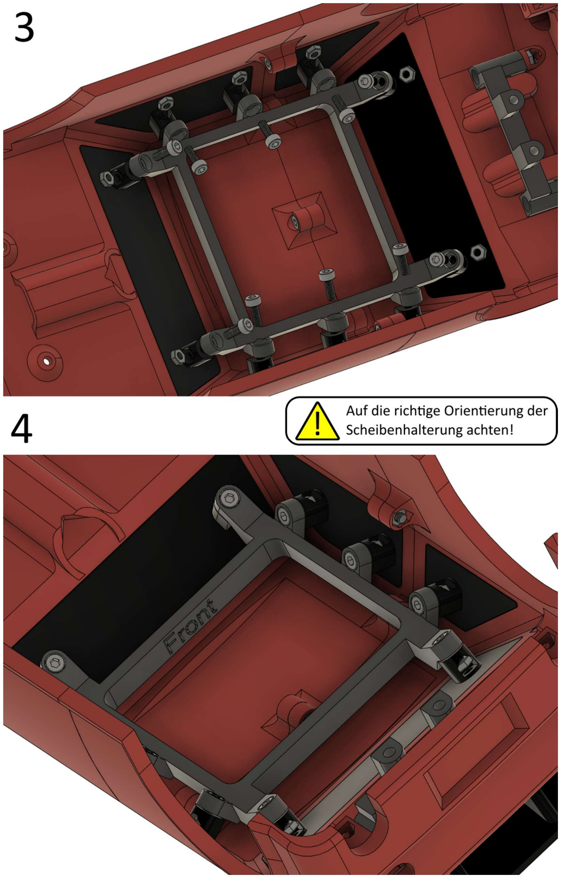
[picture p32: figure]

68

69

### 4.5.3 Frontscheinwerfer

Benötigte Bauteile: Karosserie (vorbereitet), Frontlicht-Verklemmung, LED-Einsatz vorn (2x), LED weiß (2x), LED gelb (2x), M3x8 mm Schraube (2x), M3 Mutter (2x)

70

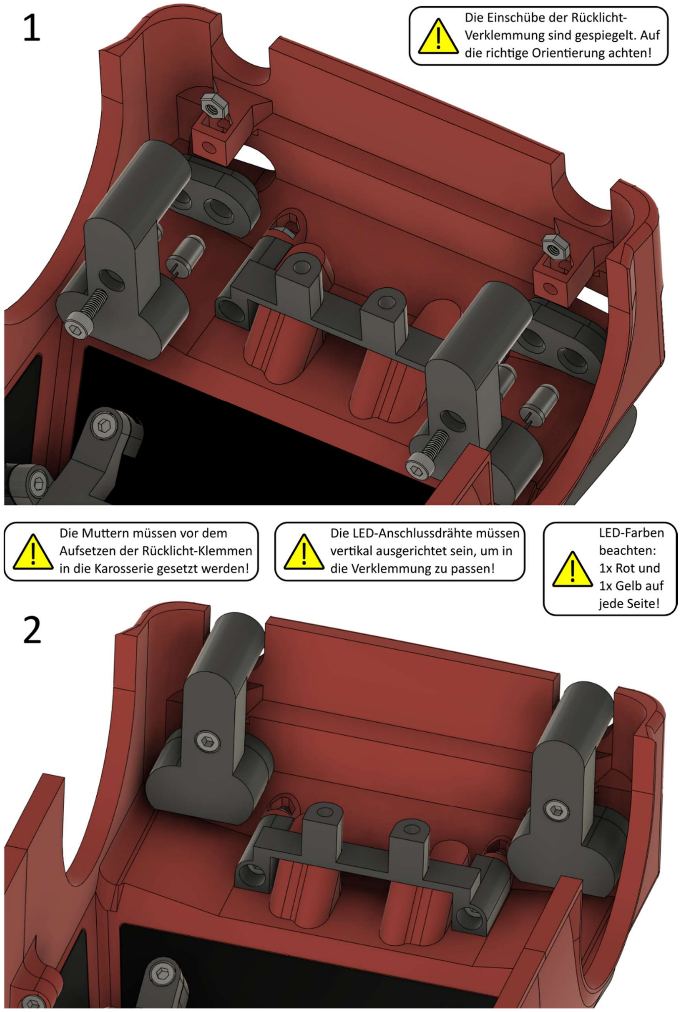
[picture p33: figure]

71

### 4.5.4 Heckscheinwerfer

Benötigte Bauteile: Karosserie (vorbereitet), Rücklicht-Verklemmung (2x), LED-Einsatz hinten rechts, LED-Einsatz hinten links, LED rot (2x), LED gelb (2x), M3x8 mm Schraube (2x), M3 Mutter (2x)

72

73

## 5. Programmierung

### 5.1 Installation Arduino IDE

EasyRC verwendet Microcontroller aus der ESP32-Familie der Firma Espressif Systems. Diese Plattform kann frei über die Arduino-Entwicklungsumgebung programmiert werden. Für die Programmierung wird deshalb die Software Arduino IDE (getestet mit Version 2.3.6) verwendet: https://www.arduino.cc/en/software/
Nach der Installation der Software muss sie für die Verwendung der ESP32-Microcontroller eingerichtet werden. Unter Datei -> Einstellungen muss unter „Zusätzliche Boardverwalter-URLs“ die Adresse https://dl.espressif.com/dl/package_esp32_index.json eingegeben werden.

Als nächstes muss der ESP32-Boardverwalter installiert werden. Dazu wird in der Symbolspalte am linken Rand des Anwendungsfensters das zweitoberste Symbol angeklickt. Dadurch önet sich die Board-Verwaltung als Sidebar. Hier muss „esp32“ eingegeben werden und im Anschluss „esp32 von Espressif Systems“ ausgewählt und installiert werden. Dabei muss die Version 2.0.17 gewählt werden (nicht die aktuelle Version!). Der Hintergrund dafür ist, dass bestimmte Programmbibliotheken im Generationswechsel von V2 auf V3 eine andere Syntax verwenden. V3 ist aber nicht so stabil wie V2, weshalb EasyRC für die ältere Version programmiert worden ist.

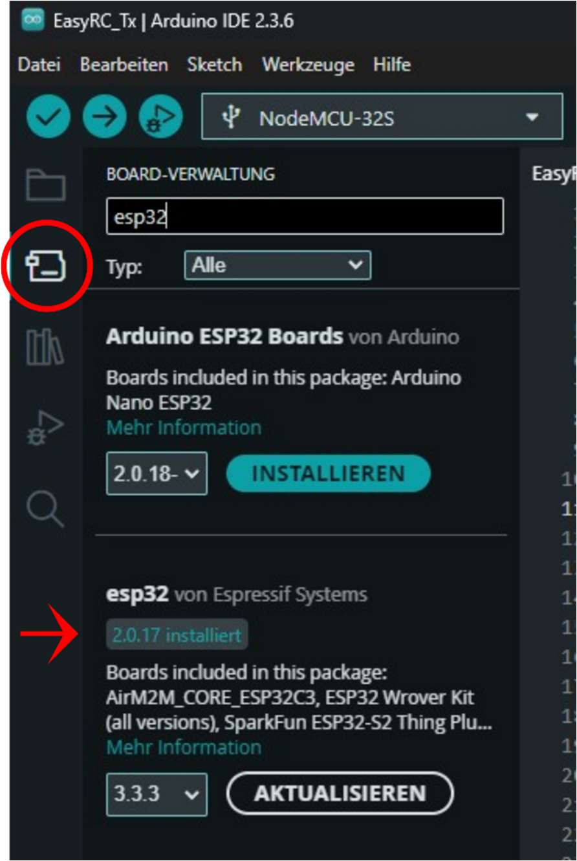
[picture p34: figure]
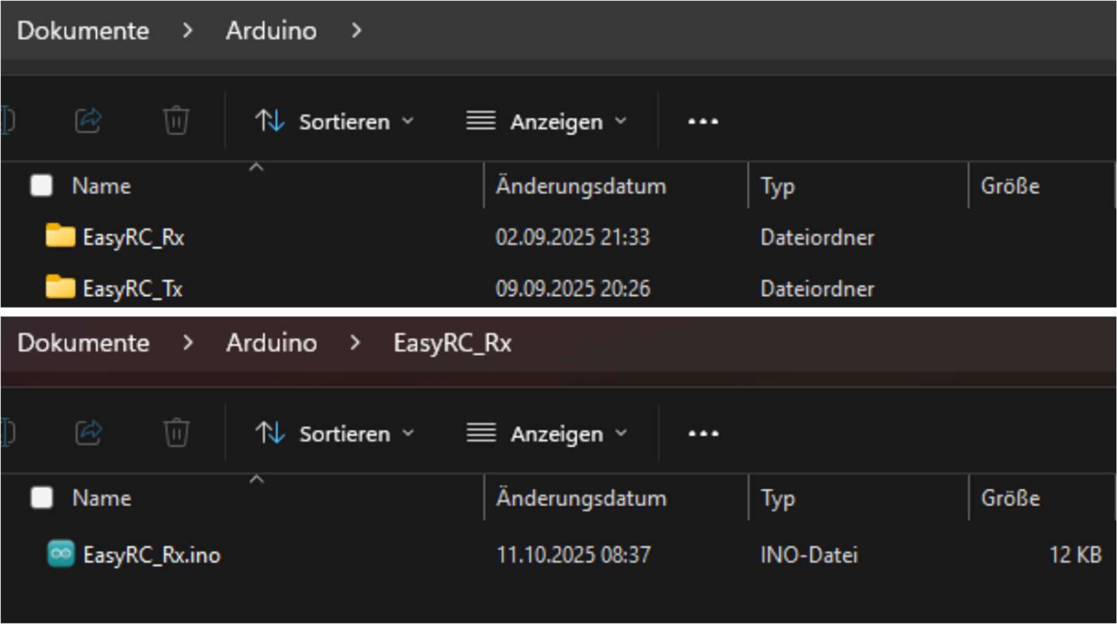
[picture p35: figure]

74

Um eine Code-Datei in Arduino IDE zu önen, muss sie in einem Ordner abgelegt sein, der denselben Namen wie die Datei trägt (ohne die .ino-Endung der Datei). Der Standard-Pfad für Arduino IDE ist in Windows Dokumente -> Arduino. Sofern keine Änderungen daran vorgenommen werden sollen, können einfach in diesem Ordner die zwei notwendigen Ordner für die EasyRC-Codes der Fernsteuerung und des Codes erstellt werden und anschließend die eigentlichen Codes dort abgelegt werden. Die Codes sind frei zum Download verfügbar unter https://github.com/TRD-B/EasyRC.

75

### 5.2 Mögliche und benötigte Code-Modifikationen

EasyRC ist so konzipiert, dass der Code des Empfängers (des Modellfahrzeugs) (EasyRC_Rx.ino) unverändert auf den Microcontroller hochgeladen werden kann, sofern keine Änderung der Geräte-Adresse (MAC-Adresse) notwendig ist. Die Geräte-Adresse muss angepasst werden, wenn mehr als ein EasyRC-System am gleichen Ort betrieben werden soll. Die Geräte-Adresse legt fest, welche Fernsteuerung welches Fahrzeug steuert (siehe dazu Kapitel 9.1). Der Code des Senders (der Fernsteuerung) (EasyRC_Tx.ino) beinhaltet einige Variablen, die modifiziert werden müssen, um das Fahrzeug zu kalibrieren. Diese sind unter dem Abschnitt „//calibration data“ im Code zu finden:

Zeile | Code | Mögliche Werte | Erklärung
15 bool | motordirection = false; | true, false | Diese Variable kehrt die Drehrichtung des Motors um. Sollte das Fahrzeug beim Bewegen des Joysticks nach vorn rückwärtsfahren, kann hier true gegen false (oder umgekehrt) ausgetauscht werden.
16 | int motorint = 10; | 1 - 20 | Diese Variable verändert, wie schnell das Fahrzeug Änderungen der Geschwindigkeit basierend auf der Joystickposition umsetzt. Ein niedrigerer Wert sorgt für eine höhere Reaktionsfreudigkeit. Ein höherer Wert verhindert ein Durchdrehen der Reifen, lässt das Fahrzeug jedoch träger auf Brems- und Beschleunigungseingaben reagieren.

76

### 18 int speedlimit =

127;

51 - 255 | Diese Variable limitiert die maximale
Geschwindigkeit des Fahrzeugs. 255 stellt die Maximalgeschwindigkeit dar. Werte kleiner als 51 (20% der Maximalgeschwindigkeit) sind zwar möglich, aber nicht zu empfehlen, da der Motor so nicht genug Kraft hat, um das Fahrzeug tatsächlich zu bewegen.
19 | int leftlimit = 358; | 308 - 410 | Diese Variable definiert den maximalen
Lenkungswinkel des Fahrzeugs nach links. Der Wert ergibt sich aus der Ansteuerung des Servomotors. Ein Wert von 308 entspricht der
neutralen | Position | (Zentrum) | des
Servomotors. | Bei | den | getesteten
Servomotoren entspricht ein höherer Wert einem Ausschlag der Lenkung nach links; das kann je nach Servomotor-Typ allerdings auch umgekehrt sein. Ein Wert von 410 entspricht dem theoretischen Maximalausschlag des Servomotors. Es sollte nicht blind der Maximalwert eingetragen werden, sondern stufenweise der maximale Ausschlag der Lenkung ermittelt werden. Der maximale Lenkwinkel ist der Winkel, bei dem die Räder noch nirgendwo an der Karosserie streifen.
20 | int rightlimit = 258; | 205 - 308 | Diese Variable definiert den maximalen
Lenkungswinkel des Fahrzeugs nach rechts (analog zum Lenkungswinkel nach links). Die neutrale Position der Lenkung ergibt sich aus dem Mittelwert des maximalen linken und maximalen rechten Lenkungswinkels. Das bedeutet, dass bei der Erhöhung eines Werts (größer als 308) der andere entsprechend verringert werden muss (kleiner als 308), um den Geradeauslauf des Fahrzeugs nicht zu verändern. Das theoretische Maximalintervall zwischen 205 und 410 für die Servo-Ansteuerung kann je nach Servomotor abweichen. Bei den getesteten Servomotoren war ein kleineres Intervall ausreichend.

77

### 5.3 Programmieren der Microcontroller

Zum Hochladen eines Codes auf einen Microcontroller muss dieser per USB an den PC angeschlossen werden. Die Fernsteuerung kann direkt über den von außen zugänglichen USB-Anschluss programmiert werden. Nachdem der Microcontroller mit dem PC verbunden worden ist, muss in Arduino IDE das richtige Modell und der richtige USB-Anschluss ausgewählt werden. Dazu muss in der oberen Leiste in das Feld mit dem USB-Verbindungssymbol geklickt werden. Daraufhin önet sich ein Dropdown-Menü, in dem auf „Wähle ein anderes Board und einen anderen Port …“ geklickt werden muss. Um den passenden Microcontroller zu finden, kann in der linken Spalte nach „Xiao“ gesucht werden. Das richtige Modell ist der „XIAO_ESP32C3“. In der rechten Spalte werden angeschlossene USB-Komponenten angezeigt. Die Nummer des Ports (COM8 im Bild) variiert je nach verwendetem USB-Anschluss des Computers. Sollte hier mehr als ein Port angezeigt werden, obwohl nur ein Microcontroller angeschlossen ist, hilft es, nicht benötigte USB-Geräte vom PC abzustecken und erneut nach aktiven Ports zu suchen.

78

Sobald das Microcontroller-Modell und der Port ausgewählt sind, kann der Code hochgeladen werden. Dazu wird in der oberen Leiste in Arduino IDE auf den nach rechts zeigenden Pfeil geklickt. Der Computer prüft daraufhin den Code auf Syntaxfehler, kompiliert ihn (Umwandlung in maschinentauglichen Code) und überträgt ihn via USB auf den Microcontroller.

Wenn das Hochladen erfolgreich ist, zeigt das Ausgabefenster schließlich den in der Abbildung gezeigten Text („Leaving… Hard resetting via RTS pin…“) an. Die USB-Übertragung ist allerdings fehleranfällig: Sollte die Übertragung abbrechen oder mit einer Fehlermeldung gar nicht erst starten, sollte der Microcontroller ab- und wieder angesteckt werden sowie geprüft werden, ob der richtige USB-Port ausgewählt worden ist. Besteht der Fehler nach mehreren Versuchen weiterhin, kann auch ein Neustart des PCs Abhilfe schaen.

79

## 6. Code der Microcontroller

Hier folgen kurze Erläuterungen zum Code der beiden Microcontroller, ohne auf die Syntax einzugehen. Es werden keine Codeabschnitte gezeigt, um das Kapitel kompakt zu halten. Die Codes können jederzeit über GitHub abgerufen werden: https://github.com/TRD-B/EasyRC

### 6.1 Fernsteuerung

Der Microcontroller der Fernsteuerung muss den Joystick auslesen, die Batteriespannung prüfen und die verarbeiteten Daten des Joysticks an das Fahrzeug schicken. Zunächst werden Programmbibliotheken eingebunden und die benötigten Variablen definiert. Außerdem wird außerhalb der Funktionen im Code definiert, wie das Datenpaket aussieht, das an das Fahrzeug übertragen wird. Danach folgt die Setup-Funktion, die einmalig beim Start des Microcontrollers ausgeführt wird und Initialisierungen vornimmt. Hier ist die Kalibration der Joystick-Achsen zu erwähnen: Beim Anschalten liest der Microcontroller mehrfach die beiden Achsen aus, um ihren Neutralpunkt zu bestimmen. Dazu werden die Pinfunktionen festgelegt und ESP-NOW initialisiert. In der permanent ablaufenden Loop-Funktion werden Unterfunktionen aufgerufen (Auslesen der Joystick-Achsen, Auslesen der Batteriespannung), geprüft, ob der Joystick-Druckknopf gedrückt ist und alle 50 ms ein Datenpaket an das Fahrzeug verschickt. Zusätzlich wird eine serielle Ausgabe erzeugt, die die aktuellen Sensorzustände zeigt, wenn ein PC angeschlossen ist.
Beim Auslesen der Joystick-Achsen wird ein kleiner Bereich um den Neutralpunkt nicht als Abweichung berücksichtigt, um ein Zittern der Lenkung und des Antriebsmotors durch Messrauschen und Toleranzen des Joysticks zu verhindern. Um die Joystick-Achsen symmetrisch zu halten, wird außerdem berücksichtigt, dass der Neutralpunkt nicht zwingend dem Mittelwert aus 0 V und 3,3 V entsprechen muss, sondern der Maximalausschlag bei einer vorgegebenen Abweichung rund um den Neutralpunkt gekappt. Das Auslesen der X-Achse (Antriebsmotor) enthält ein Segment, das den Ausgabewert invertiert. Dieses Segment wird durch das Setzen der Variable „motordirection“ (Kapitel 5.2) (de)aktiviert. Außerdem gibt die X-Achse dem Fahrzeug auch vor, wie die Helligkeit der Rücklichter (Rücklicht versus Bremslicht) eingestellt werden soll, abhängig davon, ob aktuell vorwärts gefahren/beschleunigt werden soll oder der Joystick in der Neutralposition bzw. rückwärtsgerichtet ist. Für die Y-Achse (Lenkung) wird entsprechend an das Fahrzeug weitergegeben, ob gelenkt und wenn, ob nach links oder rechts gelenkt wird, um die Blinker entsprechend ansteuern zu können.
Das Auslesen der Batteriespannung erfolgt unter Berücksichtigung des eingesetzten Spannungsteilers und lässt beim Unterschreiten eines Grenzwerts (3,4 V) einen internen Zähler ansteigen. Dieser Grenzwert ist verhältnismäßig hoch für eine LiIon-Zelle, die gefahrlos bis 3,0 V entladen werden kann, allerdings versorgt die Batterie einen im Xiao ESP32-C3 integrierten Spannungswandler, der stabile 3,3 V für den Microcontroller zur Verfügung stellen muss. Deshalb wird eine höhere Spannung benötigt. Sobald der Zähler einen vorgegebenen Wert übersteigt, wird die Batteriewarnung (blinkende LED der Fernsteuerung) ausgelöst. Hier wird ein Zähler verwendet, um die Warnung nicht bei einem einzigen Unterschreiten des Spannungsgrenzwerts auszulösen, da Messrauschen oder abrupte Bewegungen der Fernsteuerung und resultierende Spannungsschwankungen (schlechter Kontakt zwischen Batterie und Batteriehalter) so Fehlalarme auslösen könnten.
Die serielle Ausgabe gibt die aktuellen Messwerte der Eingänge des Microcontrollers aus. Dieses Codesegment ist für die Fernsteuerung nicht notwendig, stört aber den Betrieb nicht und kann zum Debuggen genutzt werden.

80

### 6.2 Fahrzeug

Der Microcontroller des Fahrzeugs muss die Daten der Fernsteuerung erhalten und darauf basierend den Lenkungsservo und den Antriebsmotor ansteuern. Zusätzlich steuert er den Piezo-Buzzer und die LEDs des Fahrzeugs an und liest die Batteriespannung aus. Im Anfangsbereich des Codes werden ebenfalls Bibliotheken aufgerufen, Variablen definiert und die Verwendung von ESP-NOW festgelegt. In der Setup-Funktion wird die Verwendung der Pins vorgegeben und ein PWM-Timer des Microcontrollers für den Servomotor programmiert (auf 50 Hz eingestellt; das ist die für RC-Servos übliche Steuerungsfrequenz). Anschließend wird ESP-NOW aktiviert und LED-Lichtsequenzen sowie Tonsequenzen des Piezo-Buzzers aufgerufen, die anzeigen, dass das Fahrzeug angeschaltet wird, auf eine Verbindung zur Fernsteuerung wartet oder dass die Verbindung zur Fernsteuerung hergestellt worden ist. In der Loop-Funktion werden Unterfunktionen aufgerufen, um die Motoren und den Piezo-Buzzer zu steuern sowie in einem größeren Codesegment die verschiedenen Alarmzustände abgefragt bzw. entsprechende Warnungen (LEDs blinken und der Piezo-Buzzer piept) beim Erreichen der Alarmzustände ausgegeben. Die Warnzustände sind ein Verbindungsabbruch zur Fernsteuerung, ausbleibende Nutzereingaben für eine längere Zeit sowie das Unterschreiten eines Batteriespannungs-Grenzwerts.
Der Verbindungsabbruch zur Fernsteuerung wird detektiert, indem bei jedem erhaltenen Datenpaket ein Timer zurückgesetzt wird (rctimer). Sollte die aktuelle Zeit die Zeit beim Erhalt des letzten Datenpakets um 1 s überschreiten, wird das als Verbindungsabbruch gewertet. Ausbleibende Nutzereingaben werden über eine Unterfunktion detektiert, die einen Timer zurücksetzt, wenn das Fahrzeug bewegt werden soll oder hupen soll. Sollte beides für 60 s lang nicht erfolgen, wird dies als ausbleibende Nutzereingaben gewertet. Die Batteriespannung wird in einer separaten Unterfunktion genau wie bei der Fernsteuerung gemessen, allerdings mit einem an die höhere Batteriespannung des Fahrzeugs angepassten Spannungsteiler und Grenzwert. Im Loop des Microcontrollers werden die Ansteuerung der Blinker sowie des Bremslichts direkt entsprechend den Eingaben durch die Fernsteuerung übernommen. Das Rücklicht als dunklere Stufe der Bremslichter wird nicht durch eine PWM-Dimmung der LEDs umgesetzt, sondern durch das abwechselnde Aktivieren und Deaktivieren bei jedem dritten Codedurchlauf. Dies ist ohne sichtbares Flackern der Rücklichter möglich, da der Microcontroller sehr schnell durch seinen Code läuft (<= 1 ms, sodass dies einer Frequenz von mehreren Hundert Hz entspricht). Die Blinker blinken im Sekundentakt (sie leuchten jede Sekunde für eine halbe Sekunde), wobei der Timer bei jedem Richtungswechsel zurückgesetzt wird, sodass der Blinker beim Einschlagen in eine Richtung immer mit einem Leuchten beginnt.
Zudem wird im Loop des Microcontrollers abgefragt, ob die Hupe des Fahrzeugs ausgelöst werden soll und entsprechend über eine Unterfunktion ein PWM-Timer und -Kanal umprogrammiert (setPWMchannel). Theoretisch sollte der ESP32-C3 über sechs voneinander unabhängig programmierbare PWM-Kanäle verfügen, allerdings war dies mit der Arduino IDE nicht umsetzbar: Sobald mehr als zwei Kanäle aufgerufen werden, kommt es zu Fehlfunktionen der PWM-Kanäle. Deshalb wird im Code ein Kanal und Timer für den Lenkungsservo reserviert und der andere je nach Bedarf einer gewünschten Tonfrequenz für den Piezo-Buzzer oder aber dem Antriebsmotor zugeordnet. Das führt zu der Einschränkung, dass das Fahrzeug nicht gleichzeitig fahren und den Piezo-Buzzer auslösen kann, sorgt aber für einen fehlerfreien Betrieb aller Komponenten. Die Tonfrequenz des Piezo-Buzzer wird über die PWM-Frequenz definiert, wobei der Kanal beim Auslösen eines Tons immer mit einem Tastgrad von 50% aufgerufen wird (Code-Unterfunktion

81

Buzzer). Für den Antriebsmotor wird eine PWM-Frequenz von 20 kHz genutzt. Die hohe Frequenz (im unhörbaren Bereich) unterbindet unerwünschte Fiep- oder Zirp-Geräusche des Motors bei Teillast.
Der Servomotor wird direkt über die eingehenden Befehle angesteuert (ServoControl), da diese bereits für die Verwendung des RC-Servos im Code der Fernsteuerung angepasst werden. Der Servomotor benötigt ein PWM-Signal mit einer Frequenz von 50 Hz, wobei der Tastgrad vorgibt, welchen Winkel der Motor einnimmt. Eine Signaldauer von 1,5 ms entspricht dem Mittelwert und das üblicherweise verwendbare Intervall reicht von 1 ms bis 2 ms. Da der PWM-Kanal für den Servomotor mit 12 bit angesprochen wird, entsprechen die 1,5 ms einem Wert von 308 (308/(2^12) mal 20 ms (50 Hz Intervall)) und die Limits liegen bei 205 und 410.
Für | den | Antriebsmotor | wird | in | einer | Unterfunktion | (setMotorSpeed) | die
Geschwindigkeitsänderung in Abhängigkeit der aktuellen Geschwindigkeit und angeforderten Geschwindigkeit geändert. Es wird bei hohen Änderungen eine Interpolation durchgeführt, die die tatsächliche Motorgeschwindigkeit langsamer ändert. Dadurch sollen übermäßig abrupte und damit für den Antriebsstrang stark belastende Eingaben verhindert werden. Die Drehrichtung wird nur geändert, wenn die Geschwindigkeit nahe Null liegt, ebenfalls um Belastungen auf dem Antriebsstrang gering zu halten.

82

## 7. Erste Schritte und Bedienung des Fahrzeugs

Wenn die Microcontroller der Fernbedienung und des Fahrzeugs programmiert worden sind, kann es schon fast losgehen! Zunächst muss aber noch die Lenkung des Fahrzeugs getrimmt werden und die Karosserie aufgesetzt werden.

### 7.1 Batterien einsetzen und Geräte anschalten

Als erstes werden Batterien in das Fahrzeug und die Fernbedienung eingesetzt. Die EasyRC-Platinen sind zwar vor Verpolung der Eingangsspannung geschützt, aber dennoch sollte man es nie auf solche Sicherungen ankommen lassen: Beim Einbau bitte immer zweimal prüfen, ob die Batterien richtigherum eingesetzt wurden. Anschließend kann die Fernbedienung angeschaltet werden. Die Status-LED der Fernbedienung leuchtet durchgehend, wenn sie ordnungsgemäß funktioniert. Sollte die LED blinken, ist die Batteriespannung niedrig. Dann muss die Batterie zunächst aufgeladen werden, bevor das Aufsetzen des Fahrzeugs weitergeht. Das ist wichtig: LiIon-Batterien reagieren empfindlich auf Tiefentladung. Sollte die Batteriespannung zu tief fallen, wird die Batterie beschädigt.
Wenn die Fernbedienung angeschaltet wird, kalibriert sich der Joystick automatisch. Die Position, die der Joystick zum Zeitpunkt des Einschaltens innehat, wird als neutrale Position hinterlegt. Deshalb darf der Joystick beim Anschalten der Fernbedienung nicht bewegt werden. Diese Kalibration wird bei jedem Start der Fernbedienung durchgeführt. Sollte man also aus Versehen den Joystick bewegt haben, muss die Fernbedienung einfach nur aus- und wieder angeschaltet werden, um wieder eine korrekte Kalibration zu erhalten. Als zweites wird das Fahrzeug angeschaltet. Da die LEDs noch nicht angeschlossen sind, wenn die Karosserie noch nicht aufgesetzt ist, gibt zunächst nur Feedback zum Status des Fahrzeugs über den Piezo-Buzzer. Er piept dreimal nach dem Anschalten (der dritte Ton ist etwas länger und höher als die ersten beiden Töne). Anschließend piept der Buzzer alle zwei Sekunden, sofern das Fahrzeug nicht mit einer Fernsteuerung verbunden ist. Sobald das Fahrzeug „seine“ Fernsteuerung findet, folgt ein Signalsequenz mit einem längeren und einem kürzeren Piepton.

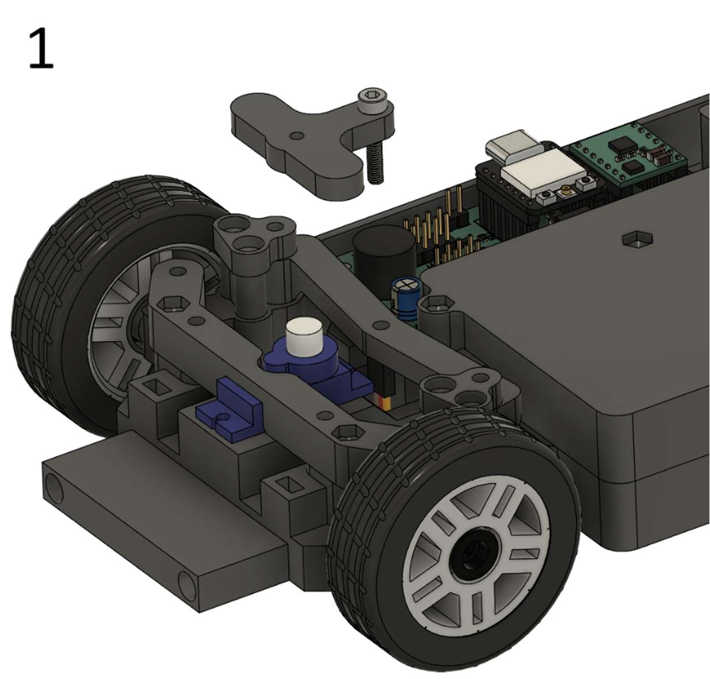
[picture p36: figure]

83

### 7.2 Lenkung fertig montieren

Zunächst zur Lenkung: Wie im Abschnitt zur Programmierung (Kapitel 5.2) erklärt worden ist, gibt es im Code zwei Variablen, die den maximalen Lenkausschlag nach links und rechts festlegen. Diese müssen angepasst werden, sodass das Fahrzeug bei neutraler Joystick-Position (bezogen auf die Achse von links nach rechts) auch tatsächlich geradeaus fährt und außerdem beim Einschlagen der Lenkung die Vorderräder nicht am Rahmen streifen (der maximale Lenkausschlag darf nicht zu groß sein).
Nun muss das Servohorn auf den Servomotor gesetzt und mit dem Lenkgestänge verbunden werden. Dieser Schritt wird erst jetzt durchgeführt, da zunächst der Servomotor seine neutrale Position einnehmen muss. Der Servomotor fährt automatisch seine neutrale Position an, wenn der Joystick der Fernbedienung nicht bewegt wird und der Mittelwert zwischen linkem und rechtem maximalen Lenkwinkel bei 308 liegt. Das ist die Ausgangslage, wenn der Code der Fernsteuerung von GitHub unverändert übernommen worden ist.
Das Servohorn wird so auf den Servomotor gesetzt, dass die Linie zwischen dem Kontaktpunkt zum Lenkgestänge und der Motorwelle möglichst parallel zur Längsachse des Fahrzeugs ist (entsprechend der roten Linie in Bild 3 der folgenden Abbildung). Da die Abtriebswelle des Servomotors ein kleines Zahnrad ist und das Servohorn in dieses Zahnrad greifen muss, kann es sein, dass das Servohorn nicht in dieser Idealline aufgesetzt werden kann. Das ist kein Problem; es sollte nur so nahe wie möglich an dieser Idealline ausgerichtet sein. Die bereits vorinstallierte M3x16 mm Schraube des Servohorn-Aufsatzes muss in die entsprechende Aussparung des Lenkgestänges geschoben werden. Schließlich muss das Servohorn noch mit einer 6 mm langen Schraube auf dem Motor fixiert werden. Die Anleitung gibt dafür eine M2.5 Schraube an, wobei der Durchmesser je nach Servotyp auch abweichen kann. Nun ist die erste Grundeinstellung der Lenkung abgeschlossen. Die feine Trimmung wird ausschließlich über die Software der Fernsteuerung durchgeführt, nachdem das Fahrzeug mit Karossiere fertig montiert ist.

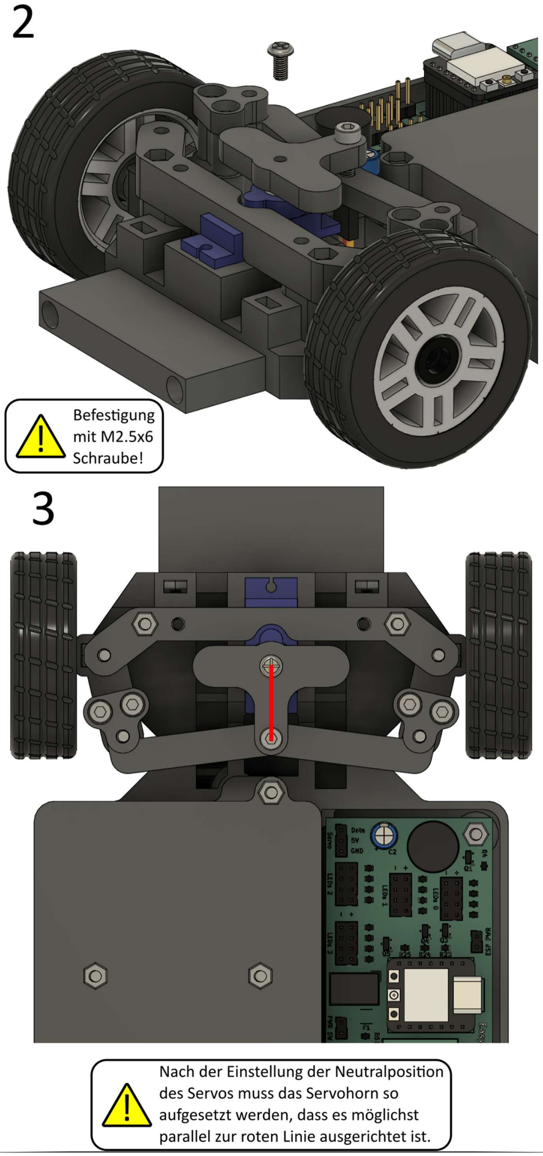
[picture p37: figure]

84

85

### 7.3 Fahrzeug fertig montieren

Nun werden die LEDs der Karosserie mit der Platine verbunden und anschließend die Karosserie auf das Chassis aufgesetzt. Die LEDs werden wie in Kapitel 4.4.4 beschrieben angeschlossen. Wichtig: Es dürfen keine Kabel beim Verschrauben der Karosserie eingeklemmt werden. Außerdem müssen die Kabel so verlegt werden, dass sie nicht an den Rädern schleifen – dabei bitte auch den Lenkausschlag der Vorderräder beachten.

86

### 7.4 Steuerungsprinzip und Funktionen des Fahrzeugs

Das Fahrzeug wird über den einzelnen Joystick der Fernsteuerung gesteuert. Wenn der Joystick nach vorn bewegt wird, beschleunigt das Fahrzeug vorwärts. Wird der Joystick nach hinten bewegt, fährt das Fahrzeug rückwärts. Sollte diese Zuordnung vertauscht sein, muss die Variable „motordirection“ im Code der Fernsteuerung modifiziert werden (siehe Kapitel 5.2).
Wenn der Joystick nach links bewegt wird, lenkt das Fahrzeug nach links; analog lenkt das Fahrzeug nach rechts, wenn der Joystick nach rechts bewegt wird. Sollte das Fahrzeug in die falsche Richtung lenken, müssen die Werte der Variablen „leftlimit“ und „rightlimit“ im Code der Fernsteuerung vertauscht werden (siehe Kapitel 5.2). Bevor die Lenkung korrekt getrimmt ist, kann es sein, dass die neutrale Lenkposition nicht korrekt ausgerichtet ist. Das wird im nächsten Kapitel eingestellt.
Die weißen Frontscheinwerfer-LEDs leuchten durchgehend, sobald das Fahrzeug angeschaltet wird. Die roten Rücklichter leuchten mit voller Intensität, solange das Fahrzeug steht oder rückwärtsfährt. Sie leuchten mit reduzierter Intensität, wenn das Fahrzeug vorwärtsfährt. Die Blinker blinken automatisch, wenn der Joystick nach links bzw. nach rechts bewegt wird. Sollte die Zuordnung der Lichter nicht passen, sollte geprüft werden, ob alle LEDs korrekt angeschlossen sind.
Der Piezo-Buzzer des Fahrzeugs fungiert als akustischer Signalgeber für Systemwarnungen und außerdem als Hupe. Wird der Joystick gedrückt, ertönt ein Signalton, solange der Joystick gedrückt bleibt. Das Fahrzeug hupt allerdings nur, während es stillsteht. Die Funktion ist deaktiviert, sobald das Fahrzeug fährt.
Die Hupe und die Blinklichter dienen außerdem zur Statusanzeige des Fahrzeugs. Neben der initialen Ton- und Lichtsequenz beim Anschalten des Fahrzeugs und der Verbindung mit der Fernbedienung (siehe Kapitel 7.1) ertönt außerdem eine Tonsequenz kombiniert mit dem Leuchten der Blinker, wenn die Batteriespannung zu niedrig ist, das Fahrzeug keine Verbindung mehr zur Fernsteuerung hat, oder aber seit längerer Zeit keine Nutzereingaben über die Fernbedienung mehr erfolgt sind. In allen drei Fällen wird der Antriebsmotor deaktiviert und kein Datensignal mehr an den Servomotor der Lenkung übertragen. Die letzten beiden Fälle sind reversibel, der Alarmzustand kann also durch eine erneute Nutzereingabe bzw. ein Anschalten/in-Reichweite-bringen der Fernbedienung deaktiviert werden. Die Warnung zur niedrigen Batteriespannung kann nur durch einen Neustart des Fahrzeugs zurückgesetzt werden.
Ursache | Ton- und Blinkfrequenz
Batteriespannung sinkt unter 10,2 V | Blinker leuchten und Hupe ertönt alle 3 s für 0,5 s
Keine Nutzereingaben für wenigstens 60 s mehr erfolgt | Blinker leuchten und Hupe ertönt alle 3 s für 1,0 s
Signalverlust zur Fernbedienung für wenigstens 1 s | Blinker leuchten und Hupe ertönt alle 3 s für 1,5 s

87

### 7.5 Trimmung der Lenkung

Zum Einstellen der Lenkung wird das Fahrzeug geradeaus bewegt, indem der Joystick nach vorn geschoben wird. Wenn das Fahrzeug auf eine Seite zieht, müssen die Variablen „leftlimit“ und „rightlimit“ angepasst werden. Der maximale Lenkausschlag wird angepasst, indem die Werte für „leftlimit“ und „rightlimit“ gleichzeitig weiter vom Servo-Mittelwert entfernt werden. Der maximale Lenkausschlag darf nicht mehr als 45° für das kurveninnere Rad betragen (siehe Abbildung). Solange der maximale Lenkausschlag noch nicht erreicht ist, kann ein Drall nach links ausgeglichen werden, indem der Wert für „rightlimit“ weiter vom Servo-Mittelwert (308) entfernt wert (analog für einen Rechtsdrall mit „leftlimit“). Wenn der maximale Lenkausschlag bereits erreicht ist, wird ein Linksdrall durch eine Annäherung des Werts für „leftlimit“ an den Servo-Mittelwert (308) ausgeglichen (analog für einen Rechtsdrall mit „rightlimit“). Die Modifikation der Lenkung kann bei aktivem Fahrzeug direkt im Code der Fernbedienung erfolgen (siehe auch Kapitel 5.2). Das erlaubt eine schnelle Anpassung ohne etwas zerlegen zu müssen.

88

### 7.6 Feintuning der Fahreigenschaften

Wenn die Lenkung eingestellt ist, ist das Fahrzeug grundsätzlich vollständig fahrbereit. Es gibt aber noch weitere Variablen, die das Fahrverhalten beeinflussen. Zunächst ist hier die Maximalgeschwindigkeit zu nennen. Diese wird ebenfalls im Code der Fernsteuerung eingestellt, über die Variable „speedlimit“ (siehe Kapitel 5.2). Der Maximalwert liegt bei 255, was einer Geschwindigkeit von bis zu ca. 10 km/h entspricht. Der Wert kann theoretisch bis auf 0 reduziert werden, allerdings skaliert die Geschwindigkeit im niedrigen Bereich nicht mehr linear mit der Vorgabe, da diese die maximale Motorspannung (eingestellt über Pulsweitenmodulation) definiert. Ein Wert von ca. 120 bis 150 stellt einen sinnvollen Kompromiss aus hoher Maximalgeschwindigkeit und guter Kontrollierbarkeit dar: Zu hohe Geschwindigkeiten bedeuten, dass Kurven und Bremsen schwierig zu meistern sind.
Eine weitere Modifikationsmöglichkeit ist die Empfindlichkeit, mit der der Motor auf Eingaben durch den Joystick reagiert. Die Variable „motorint“ im Code der Fernsteuerung (siehe Kapitel 5.2) gibt vor, wie viele Millisekunden zwischen Änderungen der Sollgeschwindigkeit vergehen. Ein niedrigerer Wert bedeutet, dass das Fahrzeug auf abrupte Joystickeingaben sehr schnell reagiert. Dieses sehr responsive Verhalten birgt den Nachteil, dass die Räder zum Durchdrehen neigen, was die Kontrollierbarkeit, insbesondere beim Bremsen, deutlich verschlechtert. Eine Erhöhung des Werts lässt den Motor hingegen träger auf veränderte Eingaben reagieren, sodass die Traktion besser wird, das Fahrzeug aber länger zum Beschleunigen und Bremsen benötigt. Als Startwert ist ein Wert von 10 voreingestellt. Dieser kann schrittweise erhöht oder reduziert werden, bis der individuell bevorzugte Kompromiss aus Reaktionsfreudigkeit und Kontrollierbarkeit gefunden ist. Die Einstellung der Werte erfolgt in der Fernbedienung, sodass das Fahrzeug wie bei der Trimmung der Lenkung nicht abgeschaltet oder zerlegt werden muss, wenn die Änderungen vorgenommen werden.

89

## 8. Mögliche Fehler und Lösungsansätze

Fehlerbeschreibung | Ursache | Lösungsmöglichkeiten
Status-LED der Fernbedienung leuchtet nach dem Anschalten nicht. | Batterie falschherum eingesetzt. | Auf korrekte Polarität achten. Anschlüsse zwischen Platine und Batteriehalter ebenfalls prüfen!
Status-LED der Fernbedienung blinkt zweimal pro Sekunde. | Batteriespannung niedrig (<3,4 V). | Batterie laden.
Status-LED der Fernbedienung flackert unruhig oder mit reduzierter Helligkeit. | Batteriespannung zu niedrig für korrekten Betrieb der Fernsteuerung (<3,0 V). | Batteriespannung prüfen. Sollte die Batterie weniger als 2,5 V haben, wurde sie tiefentladen und muss ersetzt werden. Andernfalls laden.
Es ertönt kein Signalton/es leuchtet keine LED des Fahrzeugs nach dem Anschalten. | Wenigstens eine der drei Batterien falschherum eingesetzt. | Auf korrekte Polarität achten. Anschlüsse zwischen Platine und Batteriehalter ebenfalls prüfen!
Es ertönt kein Signalton/es leuchtet keine LED des Fahrzeugs nach dem Anschalten. | Die Batterien sind defekt (alle drei zusammen liefern <7 V, also weniger als 2,3 V pro Zelle). | Batterien einzeln prüfen und tiefentladene/defekte Zellen ersetzen.
Die Tonsequenz für die Verbindung mit der Fernbedienung ertönt nicht (das Fahrzeug piept alle 2 s, obwohl eine angeschaltete Fernbedienung daneben ist). | Geräte-Adressen zwischen Fernbedienung und Fahrzeug nicht korrekt (gleich) definiert. | Die Codezeilen 27 und 28 in der Fernsteuerung und 23 und 24 im Fahrzeug müssen identisch sein. Siehe Kapitel 9.1.
Die Tonsequenz für die Verbindung mit der Fernbedienung ertönt nicht (das Fahrzeug piept alle 2 s, obwohl eine angeschaltete Fernbedienung daneben ist). | Die Antennen sind nicht ordnungsgemäß in den Anschlüssen der Microcontroller eingesteckt. | Die Antennenanschlüsse auf korrekten Sitz prüfen. Die Funkreichweite ohne die externen Antennen ist extrem gering.
Die Tonsequenz für die Verbindung mit der Fernbedienung ertönt nicht (das Fahrzeug piept alle 2 s, obwohl eine angeschaltete Fernbedienung daneben ist). | Starke Interferenzen durch WLAN. | Funkkanal der EasyRC-Plattform wechseln. Siehe Kapitel 9.2.
Das Fahrzeug fährt, obwohl der Joystick der Fernsteuerung nicht bewegt wird. | Joystick nicht korrekt kalibriert. | Fernsteuerung aus- und wieder anschalten. Dabei den Joystick nicht aus der Ruheposition bewegen.
Das Fahrzeug fährt eine Kurve, obwohl der Joystick nur nach vorn/hinten bewegt wird. | Lenkung nicht korrekt getrimmt. | Anweisungen in Kapitel 7.5 zur Trimmung der Lenkung folgen.
Das Fahrzeug fährt eine Kurve, obwohl der Joystick nur nach vorn/hinten bewegt wird und/oder lenkt nicht bei Joystick-Eingaben. | Servomotor defekt (z.B. durch eine zuvor erfolgte Kollision mit den Vorderrädern). | Servomotor austauschen und die Montage und Trimmung (Kapitel 7.2, 7.5) der Lenkung ausführen.

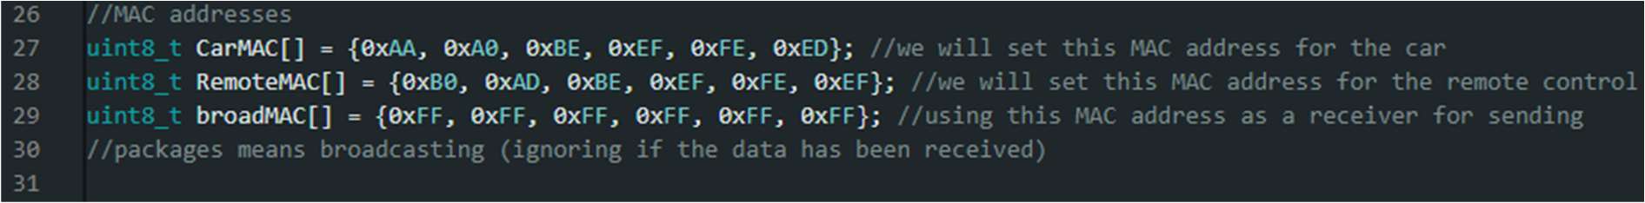
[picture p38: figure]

90

## 9. Anhang

### 9.1 Änderung der Geräte-Adresse der EasyRC-Plattform

Die Geräte-Adresse der EasyRC-Plattform kann geändert werden, um mehrere EasyRC-Systeme gleichzeitig betreiben zu können. Wichtig ist, dass immer ein Paar aus Sender und Empfänger die gleichen Geräte-Adressen hinterlegt hat: Das Fahrzeug hat die Geräte-Adresse der zugehörigen Fernsteuerung hinterlegt und prüft beim Erhalt neuer Datenpakete, ob diese von einer Fernsteuerung mit der korrekten Geräte-Adresse verschickt worden sind. Deshalb müssen die Variablen CarMAC und RemoteMAC sowohl im Code des Microcontrollers der Fernsteuerung als auch des Fahrzeugs geändert werden, wenn ein zweites EasyRC-System eingesetzt werden soll. Die Geräte-Adressen sind in der Fernsteuerung in den Codezeilen 27 und 28 hinterlegt. Im Fahrzeug sind sie in den Zeilen 23 und 24 zu finden. Die Geräte-Adresse besteht aus sechs Zeichenpaaren, die sich aus Zahlen und Buchstaben zusammensetzen. Die Abbildung zeigt die Geräte-Adressen in der Fernsteuerung. Zur Änderung der Geräte-Adressen reicht es bereits aus, lediglich ein Zeichen eines Zeichenpaars zu ändern.

Hier ist eine kleine Auswahl an möglichen Geräteadressen, die die Zeilen im Code direkt ersetzen können. Das oberste Paar entspricht den Geräte-Adressen im Auslieferungszustand. Das ausgewählte Paar muss sowohl in der Fernsteuerung als auch im Fahrzeug hinterlegt werden.

uint8_t CarMAC[] = {0xAA, 0xA0, 0xBE, 0xEF, 0xFE, 0xED}; //we will set this MAC address for the car
uint8_t RemoteMAC[] = {0xB0, 0xAD, 0xBE, 0xEF, 0xFE, 0xEF}; //we will set this MAC address for the remote control uint8_t CarMAC[] = {0xA0, 0xA0, 0xBE, 0xEF, 0xFE, 0xED}; //we will set this MAC address for the car
uint8_t RemoteMAC[] = {0xBA, 0xAD, 0xBE, 0xEF, 0xFE, 0xEF}; //we will set this MAC address for the remote control uint8_t CarMAC[] = {0xAA, 0xAA, 0xBE, 0xEF, 0xFE, 0xED}; //we will set this MAC address for the car
uint8_t RemoteMAC[] = {0xB0, 0xAA, 0xBE, 0xEF, 0xFE, 0xEF}; //we will set this MAC address for the remote control uint8_t CarMAC[] = {0xA0, 0xAA, 0xBE, 0xEF, 0xFE, 0xED}; //we will set this MAC address for the car
uint8_t RemoteMAC[] = {0xBA, 0xAA, 0xBE, 0xEF, 0xFE, 0xEF}; //we will set this MAC address for the remote control

91

### 9.2 Änderung des Funkkanals der EasyRC-Plattform

Der Funkkanal wird im Code in den Zeilen 90 und 92 (Fernbedienung, in der Abbildung gezeigt) sowie 124 und 126 (Fahrzeug) eingestellt, indem die rot markierte Zahl verändert wird. Die Voreinstellung der Plattform ist Kanal 1. Es kann ein Wert zwischen 1 und 13 ausgewählt werden. Wichtig: Ein verbundenes Paar aus Fahrzeug und Fernsteuerung muss denselben Kanal nutzen. Andernfalls ist keine stabile Verbindung möglich!

92

## 10. Noch umzusetzende Verbesserungen

- Anschluss für einen externen (beliebigen) Motortreiber: Die Fahrzeug-Leiterplatte soll um Ausgang erweitert werden, der GND sowie die zwei Pins zur Steuerung von Motor-Drehrichtung und Geschwindigkeit zur Verfügung stellt. So kann ein externer Motortreiber mit höherer Leistung genutzt werden. Alternativ könnte auch ein Ausgang mit 5 V, einem PWM-Pin sowie GND integriert werden, um beliebige Motortreiber aus dem RC-Bereich nutzen zu können. Hier besteht allerdings die Einschränkung, dass diese über eine eigene Logik verfügen, um Steuerungssignale in Drehzahl und Drehrichtung umzusetzen, die je nach Modell nur eingeschränkt (wenn überhaupt) verändert werden kann.
- Alternative Revisionen von Fahrzeug und Fernsteuerung entwickeln, die größer sind und mehr Leistungsreserven bieten.

93

## 11. Impressum

EasyRC ist eine open-source-Plattform, entwickelt von Thomas Böhm. Alle relevanten Informationen sowie Updates zum Projekt sind im zugehörigen GitHub-Respository zu finden: https://github.com/TRD-B/EasyRC
Der Autor übernimmt keine Haftung für Schäden oder Verletzungen, die durch die Nutzung der zur Verfügung gestellten Hard- und Software entstehen können!

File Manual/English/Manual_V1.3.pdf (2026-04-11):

# EasyRC – open-source RC platform

## Manual

Version 1.3; Date: 11.04.2026

2

## Contents

1. Remarks and specifications | 4
1.1 | Safety information | 4
1.2 | EasyRC specifications | 5
2. Part lists | 6
2.1 | Electronic components | 6
2.2 | Metal parts | 8
2.3 | Printed parts | 9
3. Electronics | 16
3.1 | Introduction | 16
3.2 | Circuit board manufacturing and assembly | 17
3.3 | Connecting electronic components | 18
3.4 | Component list | 19
3.5 | Overview of remote control electronics | 22
3.6 | Overview of vehicle electronics | 25
4. Assembly guide for the remote control and vehicle | 31
4.1 | Remote control | 35
4.2 | Drive train and wheels | 41
4.3 | Front wheels and steering | 51
4.4 | Finalization of the chassis | 58
4.5 | Body kit | 65
5. Programming | 73
5.1 | Installation of Arduino IDE | 73
5.2 | Possible and necessary code adjustments | 75
5.3 | Programming the microcontrollers | 77
6. Microcontroller code | 79
6.1 | Remote control | 79
6.2 | Vehicle | 80
7. First steps and operation of the vehicle | 82
7.1 | Inserting batteries and switching on the devices | 82
7.2 | Finalizing the steering assembly | 83
7.3 | Finishing the assembly of the vehicle | 85
7.4 | Control principle and functions of the vehicle | 86
7.5 | Trimming the steering | 87
7.6 | Fine-tuning the driving characteristics | 88

3

8. Possible errors and their solutions | 89
9. Appendix | 90
9.1 | Changing the hardware addresses of the EasyRC platform | 90
9.2 | Changing the radio channel of the EasyRC platform | 91
10. | Improvements to be implemented | 92
11. | Imprint | 93

4

## 1. Remarks and specifications

### 1.1 Safety information

EasyRC is an open-source platform for wirelessly controlled model vehicles, which are assembled from 3D-printed components. This manual must be read fully and understood prior to the assembly to recognize possible hazards and avoid injuries or damage.
Generally, remote-controlled vehicles are not permitted on public roads. Pilots of RC vehicles are at risk of losing control over the vehicle in case of interference or if the maximum transmission distance is exceeded. EasyRC mitigates this risk by incorporating a safety routine that turns o the vehicle's motor if no signals from the remote control are received for at least 1 s (the remote control transmits 20 data packets per second, meaning a single lost data packet cannot trigger this safety routine). However, this safety routine remains ineective if the vehicle receives interfering signals that are falsely interpreted as commands from the remote control. To this end, the vehicle checks the individual hardware address (MAC address) of the remote control that is sent with every data packet. The data is only further processed if this address matches the internally saved hardware address of the paired remote control. Therefore, it is essential to program every pair of remote control and vehicle with a unique set of hardware addresses if several EasyRC models are to be used simultaneously, meaning that one remote control will only control one vehicle. The wireless connection operates at a frequency of 2.4 GHz, which is also used for common WiFi signals. Hence, connection issues may occur in buildings with many wireless networks. If connection issues are frequent, EasyRC's radio channel can be changed. The EasyRC platform utilizes batteries with a system voltage of up to approximately 12 V DC. This voltage is generally considered harmless to humans; there is no risk of dangerous electric shocks. Furthermore, the vehicle's circuit board is protected from high currents by a fuse. Still, batteries can be damaged by improper use (e.g., overcharging, short circuits, physical damage), which may result in incineration and the release of harmful substances. Therefore, the employed lithium-ion batteries must only be charged with suitable chargers. The maximum cell voltage (charging end voltage) of a single cell equals 4.2 V. This voltage must not be exceeded! The batteries must not be used further if they are physically damaged or have been overcharged. Short circuits must be avoided. Additionally, deep discharging (<2.5 V) irreversibly damages a cell. The circuit boards of the EasyRC platform are protected against reverse polarity. However, since the vehicle requires three cells in series, the user has to carefully check for correct polarity when installing the single cells to avoid damaging the batteries. Batteries and electronic components must not be discarded as residual waste, but must be disposed of or recycled in an environmentally compatible manner based on local available options.

5

### 1.2 EasyRC specifications

### 1.2.1 Remote control

Size: 80x40x41 mm³ (LxWxH)
Weight: approx. 125 g (including battery) Microcontroller: ESP32-C3
Wireless communication: 2.4 GHz (ESP-NOW protocol) Joystick: Alps 10k (Playstation 4 model)
Power supply: 1x 18650 Li-Ion battery (3,7 V)
Power consumption: approx. 0.5 W
Notes:
- Battery connector is reverse polarity protected
- Low battery indicator (<3,4 V): LED starts blinking
- Self-calibrating joystick

### 1.2.2 Vehicle

Size: 282x125x95 mm³ (LxWxH)
Scale: 1:16
Weight: approx. 1 kg (including batteries) Microcontroller: ESP32-C3
Wireless communication: 2.4 GHz (ESP-NOW protocol)
Motor driver: Pololu DRV8876 (QFN)
Drive motor: JGA25-370 Brushed DC motor with gearbox (12 V, 1000 U/min) Speed: max. 10 km/h
Steering servo: MG90S metal-gear micro servo
Power supply: 3x 18650 Li-Ion battery (11.1 V)
Power consumption: approx. 0,8 W (idle); approx. 3-6 W (driving) Notes:
- Battery connector is reverse polarity protected
- Low battery warning (<10,2 V): Motor disabled, buzzer beeps
- Connection loss warning (> 1s): Motor disabled, buzzer beeps
- No user input warning (no inputs for >1 min): Buzzer beeps
- Self-resetting fuse in case of too high currents (>1.5 A)

6

## 2. Part lists

### 2.1 Electronic components

Figure | Designation | Description
| 1x EasyRC Tx circuit board | Circuit board with components for the remote control. Includes the joystick as well as the microcontroller that establishes the wireless connection. Component list in chapter 3.4.
| 1x EasyRC Rx circuit board | Circuit board with components for the car. Includes the microcontroller for controlling the car and the motor driver for the drive motor. Component list in chapter 3.4.
| 1x RC servo motor, type MG90S, including servo horn Color coding of the connection cable: Yellow: Data Red: +5 V Brown: GND | Motor with integrated gearbox and electronics that adjusts the output shaft within an angle interval of approx. 180° based on its input signal. The servo horn is used as a connector to the component that shall be moved and is screwed onto the servo's output shaft. Important: Verify correct polarity! Reverse polarity destroys the servo motor!
| 1x Geared DC motor JGA25-370 (1000 U/min) The cable can be color-coded: Red: +12 V Black: GND | Motor with integrated 1:10 gearbox. The motor reaches 1,000 rpm at 12 V. The motor shaft is D-shaped to allow stable power transmission. The motor's rotation direction depends on the orientation of the connector.

7

8x wired 5-mm-LED The cable should be color-coded: Red: +5 V* (long pin) Black: GND (short pin) *Only valid for EasyRC: The series resistors that are required for the LEDs are integrated in the EasyRC circuit board. | Light-emitting diodes in dierent colors (2x white, 4x yellow, and 2x red). Type: Quadrios 2111O182 (white) Quadrios 2111O171 (yellow) Quadrios 2111O172 (red) Important: Use suiciently long wires when soldering wires to the LEDs (30-40 cm) and verify correct polarity. LEDs do not work and can be damaged when incorrectly connected!
4x 18650 Li Ion battery Voltage window: 4.2 V (fully charged) 3.3 V (discharged) | Typ: Lishen LR 1865SS 3.1 Ah Lithium-ion battery for operating EasyRC. The batteries must be charged with a dedicated charger. EasyRC monitors battery voltage and warns the user when the batteries are drained.
Battery holder for single cells Required sizes: 1x 3 18650 cells 1x 1 18650 cells | Type: Battery holders with loose wires Important: Always confirm correct polarity before inserting cells! The batteries and connected components may be damaged by reverse polarity.
1x On/o switch | Type: Marquardt 01801.1148-02 Switches the vehicle on and o.

8

### 2.2 Metal parts

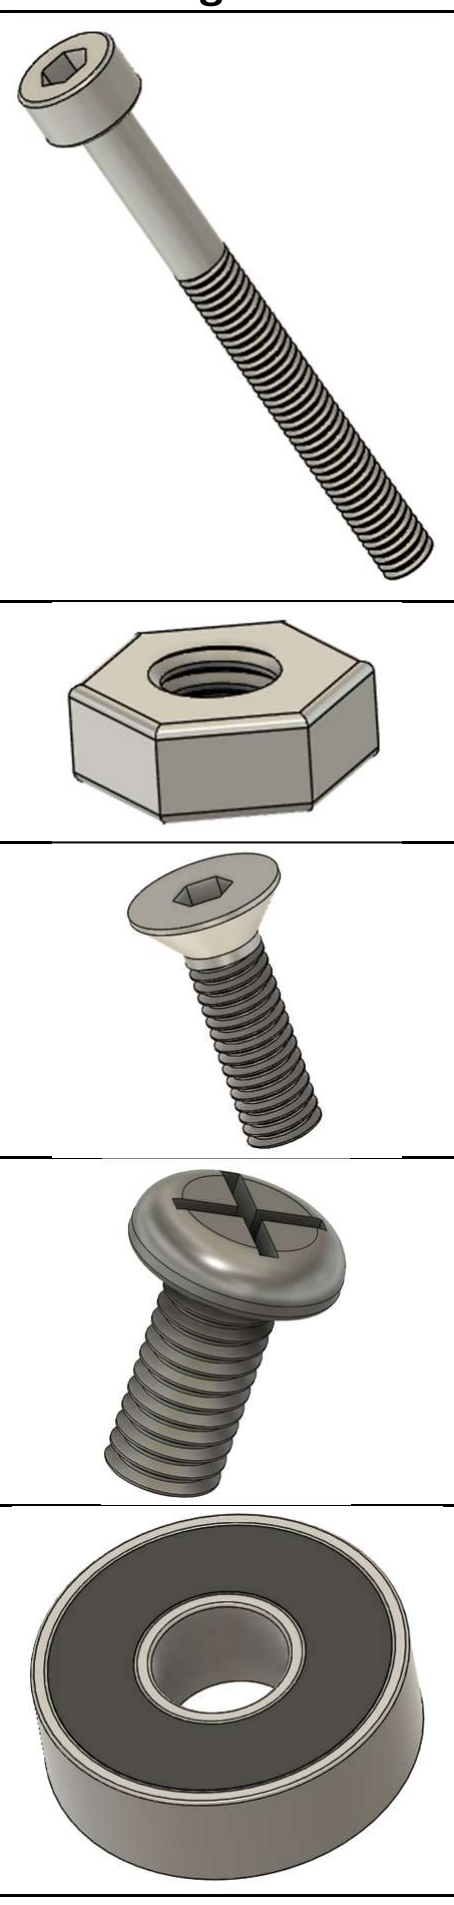
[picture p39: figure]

Figure | Designation | Description
| M3 cylinder head screw Required sizes: 29x M3x8 mm 11x M3x16 mm 8x M3x20 mm 21x M3x30 mm | Screw with metric 3 mm threading. A 2.5 mm hex key drives the head.
| 64x M3 hex nut | Nut for screws with metric 3 mm threading.
| M3 countersunk screw Required size: 3x M3x10 mm | Screw with metric 3 mm threading. A 2.0 mm hex key drives the head.
| M2.5 screw Required size: 1x M2.5x6 mm | Screw with metric 2.5 mm threading. Required to connect the servo horn to the servo motor.
| Ball bearings Required types: 4x 605 (5x14x5 mm) 4x 608 (8x22x7 mm) 2x 6802 (15x24x5 mm) | The sizes of the bearings are described by the inner diameter x outer diameter x height.

9

### 2.3 Printed parts

Orientations given in the hints column always refer to the part's orientation with respect to the complete model, not the orientation shown in the figure column.

Figure | Designation, chapter | Hints for printing
| 1x Remote control lower intermediate frame Chapter 4.1.1 | Upper side toward the print bed; support is recommended.
| 1x Remote control top Chapter 4.1.2 | Bottom toward the print bed; support is required (organic support recommended).
| 1x Remote control upper intermediate frame Chapter 4.1.2 | Bottom toward the print bed; support is not needed.
| 1x Remote control bottom Chapter 4.1.2 | Upper side toward the print bed; support is not needed.

10


1x Remote control joystick extension Chapter 4.1.3 | Upper side toward the print bed; support is not needed.
1x Remote control battery cover Chapter 4.1.3 | Bottom toward the print bed; support is not needed.
1x Motor gear (25 teeth) Chapter 4.2.1 | Gear with flat side toward the print bed (should be printed as a single part).
1x Intermediate gear (16 teeth) with 2x bearing mount. Chapter 4.2.2 | Gear with flat side toward the print bed (should be printed as a single part). Bearing mount with the outer side toward the print bed. No support needed.
1x Dierential gear (24 teeth) with spacer ring. Chapter 4.2.3 | Gear with flat side toward the print bed (should be printed as a single part).

11

2x Crown gear (15 teeth) Chapter 4.2.3 | Gear is required twice. Print with the teeth facing upward. Support is mandatory!
2x Crown gear (10 teeth) with 1x spacer Chapter 4.2.3 | Gear is required twice. Print with the teeth facing upward. No support needed.
2x Dierential case Chapter 4.2.3 | The dierential case is required twice. Print with the outside facing upward. Support is mandatory (organic support is recommended).
2x Rear rim with tire and spacer Chapter 4.2.4 | Print rim with the outside facing toward the print bed. Support is required. Print the spacer with the inside facing toward the print bed. Print the tire from very soft TPU if possible.

12

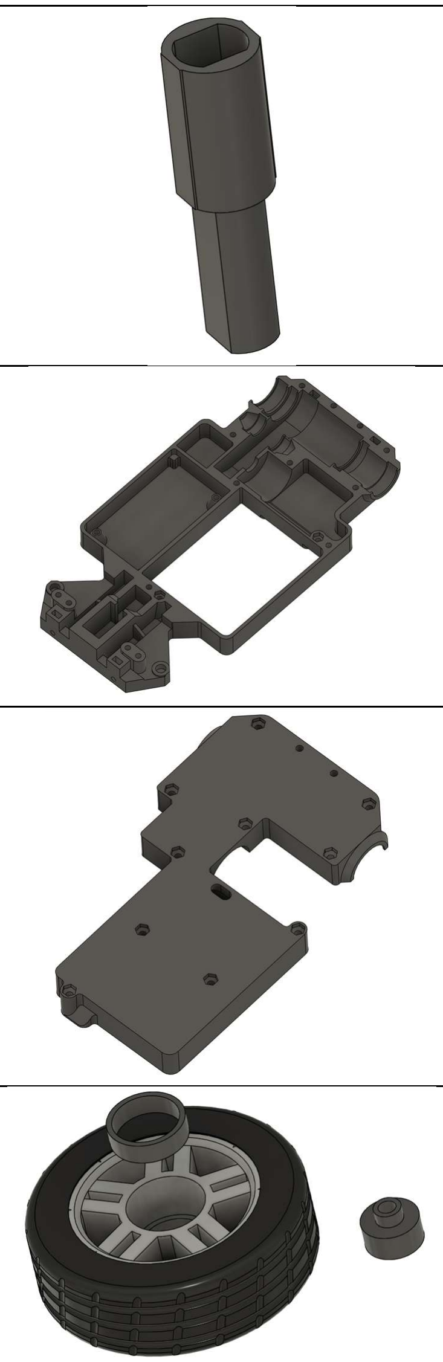
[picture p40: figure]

2x Rear axle (in two versions with 2.5 mm length dierence) Chapter 4.2.4 | Axles should be printed from TPU (hard TPU is recommended). Print axles with the flattened side toward the print bed. No support needed.
1x Chassis bottom Chapter 4.2.5 | Bottom side toward the print bed. Support is needed.
1x Chassis top Chapter 4.2.5 | Upper side toward the print bed. No support needed.
2x Front rim with tire, locking ring, and spacer Chapter 4.3.1 | Print rim with the outside facing toward the print bed. Print spacer with the outside facing toward the print bed. Support is required for both components. Print the tire very soft TPU if possible.
2x Front wheel mount (mirrored versions for left and right) with spacer and steering linkage connector Chapter 4.3.1, 4.3.2 | Print front wheel mount with the bottom toward the print bed. Steering linkage connector with the upper side toward the print bed. Spacer with the inside toward the print bed. No support needed.

13

1x Steering linkage Chapter 4.3.2 | Upper side facing toward the print bed. No support needed.
1x Chassis securing bracket Chapter 4.3.3 | Upper side facing toward the print bed. No support needed.
1x Battery lid Chapter 4.4.2 | Bottom facing toward the print bed. No support needed.
1x Rear bumper Chapter 4.4.3 | Upper side facing toward the print bed. No support needed.
1x Front bumper Chapter 4.4.3 | Bottom facing toward the print bed. No support needed.

14

1x Servo horn attachment Chapter 4.4.5 | Upper side toward the print bed. No support needed. Print from TPU. The attachment is available in a large and a small version. The version that fits the servo horn has to be printed (see 4.4.5).
1x Rear body Chapter 4.5.1 | The side that connects to the front body has to face the print bed. Organic support is required. Activate the brim to improve adhesion.

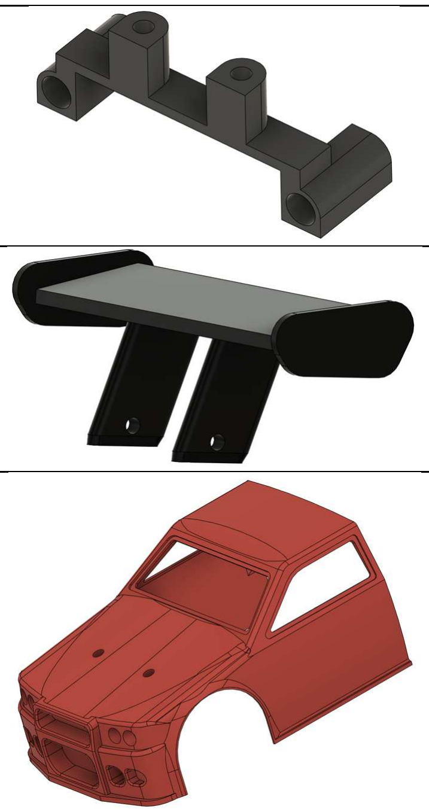
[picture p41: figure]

1x Rear wing holder Chapter 4.5.1 | Inner side (the side that is oriented toward the vehicle's front) facing toward the print bed. No support needed.
1x Rear wing Chapter 4.5.1 | Rear side toward the print bed. Support required. Activate the brim to improve adhesion.
1x Front body Chapter 4.5.2 | The side that connects to the rear body has to face the print bed. Organic support is required. Activate the brim to improve adhesion.

15

Windows (1x front, 1x left front, 1x left rear, 1x right front, 1x right rear, 1x rear) Chapter 4.5.2 | Print windows with the outside toward the print bed. No support needed.
1x Window holder Chapter 4.5.2 | Upper side facing toward the print bed. Support is recommended.
1x Front light clamp with 2x LED insert Chapter 4.5.3 | Print the front light clamp with the upper side toward the print bed. Support is required. Print LED inserts with their inner sides (facing the light clamp) toward the print bed. The LED insert is required twice.
2x Rear light clamp and exhaust with LED insert (LED insert in mirrored versions for left and right) Chapter 4.5.4 | Print the rear light clamp and LED inserts with their inner sides (the sides facing the vehicle's front) toward the print bed. No support needed. The clamp is needed twice.

16

## 3. Electronics

### 3.1 Introduction

EasyRC utilizes the ESP32 microcontroller for the remote control, which detects user inputs via the joystick and sends them wirelessly to the vehicle. The vehicle incorporates another ESP32 microcontroller to receive these data packets and convert them into commands for the steering and drive motors. A small developer board, the Xiao ESP32-C3 from SEEEDStudio is used because this platform includes all required components to program the microcontroller (via USB-C), to provide 3.3 V power to the microcontroller from higher input voltages, and because it provides easily accessible pins to connect to peripherals. The ESP32 is ideally suited for such a system because it is an inexpensive microcontroller that oers all required functions without having to use additional chips: It not only includes digital inputs and outputs (to read simple switches and output on/o commands) but also analog inputs to read sensors with non-discrete measurement signals and convert them into digital data. To this end, it incorporates analog-digital converters that convert variable measurement signals, such as a joystick axis, into processable numbers for the microcontroller at high resolution.
Furthermore, it oers PWM-compatible outputs, allowing for equally fine control of the steering servo and the drive motor. PWM is the abbreviation for pulse width modulation and is a means to transmit a finely dierentiated signal via a digital pin that can only output 0 and 1 by considering the time component (for how long per output time interval is the output set to 0 and 1? ("PWM duty cycle")). Here, the ESP32 can adjust the output time interval, also referred to as PWM frequency, over a very broad range. It can apply dierent frequencies to dierent output pins simultaneously. Lastly, the ESP32 features a module for wireless communication. It transmits at 2.4 GHz and, thus, can communicate with standard WiFi networks. In this case, this option is not used, but the proprietary ESP-NOW communication protocol of the ESP32 is employed. This protocol enables establishing a connection between two ESP32 microcontrollers, regardless of the presence or absence of WLAN, allowing the remote control to send its data packets directly to the vehicle. Furthermore, the Xiao ESP32-C3 developer board comes with an external antenna. This antenna must be installed to achieve the required radio range for a remote-controlled vehicle. Thus, the ESP32 includes all base functions to be used as a radio and control unit for the EasyRC platform. Nonetheless, circuit boards are needed that contain additional components to allow the remote control and vehicle to be used. For example, the LED lighting in the car uses transistors as switches because the LEDs require more current than the microcontroller can provide directly. It switches a separate power supply for the LEDs using the transistor. The drive motor requires a separate motor driver that accomplishes a similar task to the transistor for the LEDs, but it must do even more than that. It allows adjusting the drive direction and speed of a brushed DC motor by using only two pins (one sets the direction and the other sets the speed). Furthermore, some smaller additions, such as resistors used as voltage dividers to allow the ESP32 to read battery voltages, or a transistor-based reverse polarity protection that prevents the boards from harm in case of an incorrectly connected battery, are included.

17

### 3.2 Circuit board manufacturing and assembly

The production files for the printed circuit boards are available on GitHub (https://github.com/TRD-B/EasyRC). They can be ordered from PCB manufacturers such as JLCPCB, PCBWay, or Aisler and then assembled with the required components. Here, lead-free solder shall be used (health protection!). The components are mostly SMD parts, which means devices that are placed on top of the circuit board and then soldered onto it. This process is a bit trickier than for THT components, whose pins are pushed through holes in the board and soldered on their bottom side, because the SMD parts are not kept in place mechanically during soldering. On the other hand, SMD components are smaller than comparable THT components, which allows circuit boards to be kept more compact. Further, only SMD part sizes large enough to allow hand soldering without special tools are used (smallest size: 0805 (2 mm x 1.25 mm)).
As a general rule of thumb for assembling a PCB, start with the smallest SMD component. Then, increasingly larger components are soldered to the board, and the THT parts are added only in the end. This way, no already soldered component can act as an obstacle in subsequent steps. For comfortable soldering, a "helping hand" - a holder with flexible arms - is recommended. The SMD parts can be soldered most easily by holding them with a pair of tweezers with delicate tips and then soldering their first contact pad. As soon as they are fixed at one point, the tweezers are no longer needed to keep them in place, and the remaining contact pads can be soldered. Importantly, when soldering the remaining contact pads, the first contact must not be melted again, as it would then become loose again instantly. The required SMD components can be easily oriented on the board. Resistors and ceramic capacitors have only two contacts and are non-polarized, meaning they do not require a specific mounting direction. The transistors have three contacts, but due to their geometry, they cannot be oriented incorrectly (when the three pins are in touch with the pads on the circuit board, the transistor is oriented correctly).
On the other hand, the THT components require more attention regarding the corrected mounting orientation. The piezo buzzer is marked with "+" at one side, and the electrolytic capacitors are also polarized components, which means they have to be placed with the anode (short pin) to the positive side and the cathode (long pin; white broad stripe on the case with a black "-") to the negative side. The same holds true for LEDs, whose pins are also polarized (anode short, cathode long). When soldering the pin headers required to connect external components to the board, a female header strip can be used as an aid to keep the pin header vertical during the soldering process. Alternatively, fine tweezers can also be used. Finally, the large components (joystick module of the remote control, DC-DC converter, piezo buzzer, and electrolytic capacitors on the vehicle's board) should be soldered.
After assembling the PCBs, the contacts must be checked. Each connection needs to be mechanically stable (pushing them gently with a finger must not detach the component), and there must not be any solder bridges between dierent contacts (solder that forms an unwanted connection between adjacent pads on the board). Only after confirming correct soldering by visual inspection should the ESP32-C3 developer boards and the motor driver be pushed into their headers on the boards and connected to power. When adding these smaller boards to the EasyRC PCBs, the correct orientation must be verified, as incorrect (180° rotated) mounting can result in malfunction and damage to the components.

18

### 3.3 Connecting electronic components

The connection between external electric components (see Chapter 2.1) and the circuit boards should be established with 0.25 mm² diameter copper wire. This diameter is more than suicient for, e.g., the LEDs, but it is also suitable for the drive motor and the on/o switch of the vehicle. Hence, only one wire size is required. It is recommended to use single-stranded copper wire with two dierent isolation colors, namely red and black. Black is commonly used to connect the negative side, and red is typically used to connect the positive side, which helps to connect polarized components without problems.
The electronic components are soldered to the copper wires and receive crimp connectors (female 2.54 mm DuPont connectors) at the end of the wires, which allows to (un)plug them easily. When crimping connectors to the wires, care must be taken to ensure the connection is mechanically stable: Even when pulling the wire, it must not loosen and slip out of the crimp pin. Depending on the crimping tool, the wire and the isolation are either crimped in one action or two separate steps are needed for both processes. If both are crimped at the same time, it may happen that the isolation is not crimped with suicient force, meaning the connection has to be finalized with pliers to ensure the pin can be pushed into the pin housing without resistance. The images below show the Xiao ESP32-C3 as it is required for the remote control. The antenna needs to be connected to the vehicle's microcontroller, too, but only the microcontroller for the remote control requires soldering wires to the power supply pads on the board's bottom. For the remote control, the wires between the ESP32-C3 and the board, as well as between the battery holder and the board, must be kept short so that the case can be closed easily (see also Chapter 4.1.1). For the car, the cables should be kept a bit too long rather than too short, as the wires can be sorted more easily. Especially for the LEDs mounted in the vehicle's body, long enough wires are needed to allow for the attachment and removal of the body without inadvertently unplugging the LEDs. The motor and on/o switch of the car do not require color-coded wires because the connection orientation of the switch does not matter, and the rotation direction of the motor, which depends on its polarization, can be easily corrected in the remote control's code (Chapter 5.2).

19

### 3.4 Component list

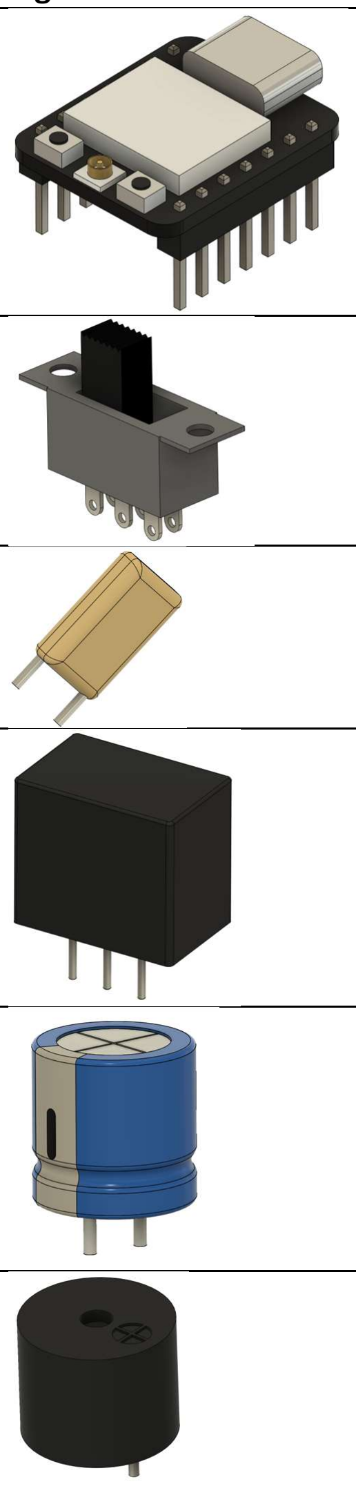
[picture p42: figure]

Figure | Designation | Description
| 2x Microcontroller development board | Type: SEEED Studio Xiao ESP32-C3
| 1x Miniature slide switch | 6 pins, type Wentronic S 166. Slider height: 6-10 mm
| 1x Self-resetting PTC fuse, 3 A | Type: ESKA FRG300-16F
| 1x DC-DC converter, 5 V 1 A | 3-pin form factor, pin compatible with LMxx linear regulators Type: Traco TSR1-2450E
| Electrolytic capacitor, 2x 25 V 100 µF 1x 25 V 22 µF | 100 µF: 6.3 mm diameter, 2.5 mm pitch (type: Panasonic EEUFM1E101) 22 µF: 5 mm diameter, 2.5 mm pitch (type: Panasonic EEAFC1E220H)
| 1x Piezo buzzer | 12 mm diameter, 6.5 mm pitch Type: HITPOINT PB1220PE05Q
| 1x 5mm wired LED, green | Type: Quadrios 2111O169

20

1x motor driver breakout board | Type: Pololu DRV8876QFN
6x MOSFET n-channel, 17 A 55 V | Form factor: TO-251AA Type: Infineon IRLU 024N
1x Zener diode, 8.2 V | Form factor: DO-41 (DO-204AL) Type: SEMTECH BZX85C8V2 R0
1x Schottky diode, 20 V 1 A | Form factor: DO-41 Type: Taiwan Semiconductor 1N 5817
Resistor, 0.6 W Required resistance values: 1x 330 Ohm 16x 470 Ohm 4x 1 kOhm 1x 10 kOhm 3x 22 kOhm 2x 33 kOhm 2x 100 kOhm | Form factor: THT 0207 Type: Yageo MF0207FTE52
Joystick module (compatible with PS4 controller) | Type: ALPS 10kOhm
Pin header, 2.54 mm pitch Required sizes: 1x 1x4 (angled) 4x 1x2 (straight) 1x 1x3 (straight) 4x 2x4 (straight) | Type: W+P 946-14-004-00 (1x4 angled) MPE 087-1-002-0-S-XS0-1260 (1x20, can be cut) MPE 087-2-040-0-S-XS0-1260 (2x20, can be cut)

21

Socket strip, 2.54 mm pitch.

Required sizes:
4x 1x7 (8.5 mm height)
2x 1x7 (5 mm height)

Type: MPE 094-1-007-0-NFX-YS0 (8.5 mm height)
Frei BL 1X10G 2,54 (5 mm
height, has to be cut to a size of 1x7)

The remote control requires shorter sockets to maintain the overall height of the board at a smaller size. Therefore, the pins of the
microcontroller board for the remote control need to be
shortened by 2-3 mm to fit into the shorter sockets.

22

### 3.5 Overview of remote control electronics

### 3.5.1 Circuit diagram

Net assignments:
+BATT: battery anode (1S LiIon)
+VDC: battery anode after on/o switch
+3V3: regulated 3.3 V (DC-DC converter integrated in Xiao ESP32-C3) -BATT: battery cathode
GND: battery cathode after reverse polarity protection

23

Explanations of the circuit snippets:
- Microcontroller: Encompasses the inputs and outputs of the Xiao ESP32-C3. The battery voltage is reduced via a voltage divider at pin D0, allowing for a safe measurement using the microcontroller's analog input. Pins D1 to D3 are connected to the joystick module. As only the pins D0 to D2 are capable of analog measurements, D1 and D2 are used for measuring the two axes of the joystick. D3 is used as a digital input for the push button. The LED at pin D7 is used with a series resistor to prevent burning the LED or damaging the microcontroller by drawing too much current (the current draw should not exceed 10 to 15 mA). The available functions of the pins of this microcontroller can be studied in detail here:
https://wiki.seeedstudio.com/XIAO_ESP32C3_Getting_Started/#
- Connectors: Shows the dierent inputs and outputs of the circuit board. The miniature slide switch has two galvanically isolated switches. Only one is required to switch the power supply to the board on and o. The 4-pin connector is used to connect the board to the battery and to the power supply pads on the bottom side of the Xiao ESP32-C3. These power supply pads enable powering the microcontroller from a single Li-ion battery, as the development board includes a voltage divider that generates a stable 3.3 V from the battery voltage.
- Reverse polarity protection: Reverse polarity protection is enabled by an "inversely" connected n-channel MOSFET between the cathode of the battery and the circuit board. This layout results in the board being powered from the battery through the transistor's body diode when the battery is correctly connected. As soon as this happens, a positive voltage is also applied to the transistor's gate, meaning it is turned on, and the voltage loss through the body diode diminishes. If the battery is connected incorrectly, the body diode of the transistor blocks current, and a negative voltage appears at the transistor's gate (+VDC equals the negative battery voltage), preventing any current from flowing between the source and drain. Hence, this transistor acts as an ideal diode.
- Joystick module: The two potentiometers of the joystick are supplied with 3.3 V from the ESP32-C3, allowing their analog outputs to generate a measurable voltage between the logic level (3.3 V) and common ground (0 V). The push button is connected to common ground and the microcontroller, which allows it to be read as 0 or 1 using an internal pull-up resistor (depending on whether the button is pressed or not).

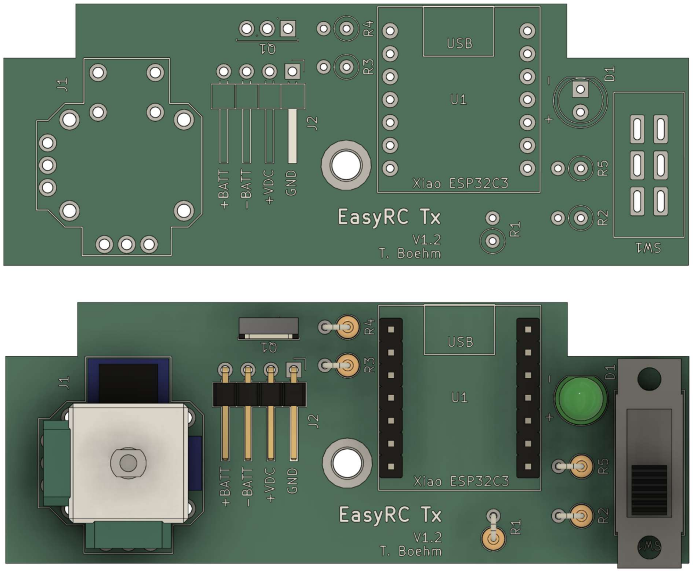
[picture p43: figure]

24

### 3.5.2 Printed circuit board

Designation | Component
D1 | 5 mm LED, green
J1 | Alps 10k joystic module
J2 | 1x4 2.54 mm angled pin header
Q1 | TO-251AA MOSFET IRLU 024N
R1 | 0207 resistor 33 kOhm
R2 | 0207 resistor 33 kOhm
R3 | 0207 resistor 10 kOhm
R4 | 0207 resistor 100 kOhm
R5 | 0207 resistor 330 Ohm
SW2 | Wentronic S 166 6 pin miniature switch
U1 | 2x 1x7 2.54 mm socket strip (5 mm height)
Remark: Verify the PCB revision!

A photograph of the PCB with the mounted microcontroller and connected battery holder is depicted in Chapter 4.1.1.

25

### 3.6 Overview of vehicle electronics

### 3.6.1 Circuit diagram

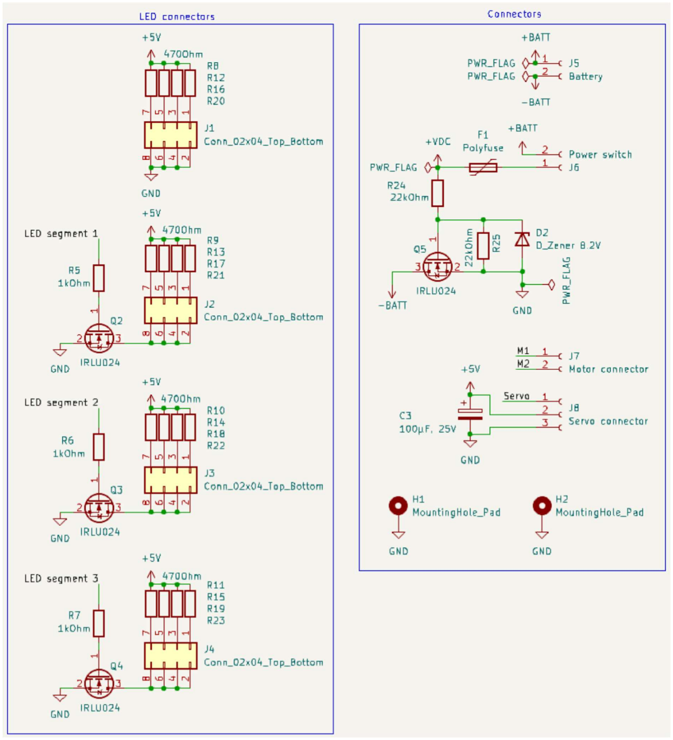
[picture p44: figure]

26

Net assignments:
+BATT: battery anode (3S LiIon)
+VDC: battery anode after on/o switch
+5V: regulated 5 V (DC-DC converter)
+3V3: regulated 3.3 V (DC-DC converter integrated in Xiao ESP32-C3) -BATT: battery cathode
GND: battery cathode after reverse polarity protection

27

Explanations of the circuit snippets:
- Microcontroller: Encompasses the inputs and outputs of the Xiao ESP32-C3. The battery voltage is reduced by a voltage divider at pin D2 to allow a safe measurement using the microcontroller's analog input. The pins D1, D3 to D7, and D10 are used as outputs. D1, D6, and D10 are used as PWM outputs, while the other pins are used as simple digital outputs. Pin D10 (PWM control of the drive motor) is connected to resistor R4, which is an optional pulldown resistor. Uncontrolled motor movements during the startup of the microcontroller (while pin D10 is still floating) can be prevented by adding a resistor with a resistance between 10 kOhm and 100 kOhm here. The 5 V input of the microcontroller is protected by a Schottky diode, which oers reverse current protection. This diode prevents current from flowing to the board when the USB port of the microcontroller is in use, as the board could overload the USB output of a computer. A capacitor is connected near the microcontroller's 5 V input to minimize voltage fluctuations and ensure stable operation.
- DC-DC conversion: Depicts the step-down converter that generates a stable 5 V from the 3S Li-ion battery to power the microcontroller, steering servo, LEDs, and piezo buzzer.
- Motor driver: The Pololu motor driver breakout board receives data from the microcontroller via two pins (speed and rotation direction). The other pins of the driver are directly connected to logic voltage, common ground, or are unconnected. A capacitor is added near the motor driver to maintain a stable voltage during rapid load changes of the drive motor. The motor is connected to the output pins M1 and M2 of the driver. Information on the pinout and control of this motor driver can be found here: https://www.pololu.com/product/4037
- Buzzer: The piezo buzzer generates noises with specific frequencies when an alternating voltage is applied. To this end, a PWM output of the microcontroller is employed, which means the voltage at the buzzer alternates between 0 V and 5 V. The frequency is given by the PWM frequency of the microcontroller, which thereby defines the tone pitch of the piezo buzzer. The buzzer is specified for use with a 5 V power supply and requires more current than the microcontroller can provide. Therefore, a transistor is used as a switch, which is turned on and o by the PWM output of the microcontroller.
- LED connectors: The LED connectors on the board are divided into four groups, each with four connectors. LED segment 0 cannot be controlled by the microcontroller but receives power permanently. This segment is designed for the headlights. Segments 1 to 3 are controlled by the microcontroller using a transistor (similar to the piezo buzzer) and serve as indicator and brake lights. Every LED output includes a separate series resistor to limit the current flowing through each LED. A resistance of 470 Ohm is recommended, but this value can be adjusted to control the LED brightness (do not exceed the specified maximum current of the LED and consider the specified maximum heat dissipation of the series resistors).
- Connectors: Shows the connectors on the board as well as its reverse polarity protection. The positive battery connector is connected to the on/o switch, which then supplies power to the board. Here, a fuse is added that trips if the current exceeds a certain limit. Furthermore, the same reverse polarity protection concept used in the remote control's board is employed. Here, a voltage divider at the gate of the transistor is used as a safety measure, as it is specified for a maximum gate voltage of 16 V, which is close to the up to

### 12.6 V supply voltage when the batteries are fully charged. The voltage divider cuts this

voltage in half to remain in a safe range. Furthermore, a Zener diode is added as an

28

additional safety measure to protect the transistor in case of inductive voltage peaks. Also, a capacitor is connected near the steering servo connector to minimize voltage drops caused by load changes in the steering motor.

29

### 3.6.2 Printed circuit board

30

Designation | Component
BATT | 1x2 2.54 mm pin header
BZ1 | Piezo buzzer (12 mm, 6.5 mm pitch)
C1 | Electrolytic capacitor, 6.3 mm, 2.5 mm pitch, 100 µF, 25 V
C2 | Electrolytic capacitor, 5 mm, 2.5 mm pitch, 22 µF, 25 V
C3 | Electrolytic capacitor, 6.3 mm, 2.5 mm pitch, 100 µF, 25 V
D1 | DO-41 Schottky diode 20 V 1 A
D2 | DO-41 Zener diode 8.2 V
F1 | PTC fuse 3 A (ESKA FRG300-16F)
LEDs 0 | 2x4 2.54 mm pin header with 4x 0207 resistor 470 Ohm
LEDs 1 | 2x4 2.54 mm pin header with 4x 0207 resistor 470 Ohm
LEDs 2 | 2x4 2.54 mm pin header with 4x 0207 resistor 470 Ohm
LEDs 3 | 2x4 2.54 mm pin header with 4x 0207 resistor 470 Ohm
Motor | 1x2 2.54 mm pin header
PWR SW | 1x2 2.54 mm pin header
Q1 | TO-251AA MOSFET IRLU 024N
Q2 | TO-251AA MOSFET IRLU 024N
Q3 | TO-251AA MOSFET IRLU 024N
Q4 | TO-251AA MOSFET IRLU 024N
Q5 | TO-251AA MOSFET IRLU 024N
R1 | 0207 resistor 100 kOhm
R2 | 0207 resistor 22 kOhm
R3 | 0207 resistor 1 kOhm
R4 | (optional) 0207 resistor 10-100 kOhm
R5 | 0207 resistor 1 kOhm
R6 | 0207 resistor 1 kOhm
R7 | 0207 resistor 1 kOhm
R24 | 0207 resistor 22 kOhm
R25 | 0207 resistor 22 kOhm
Servo | 1x3 2.54 mm pin header
U1 | DC-DC converter Traco TSR1-2450E
U2 | 2x 1x7 2.54 mm socket strip (8.5 mm height)
U3 | 2x 1x7 2.54 mm socket strip (8.5 mm height)
Remark: Verify the PCB revision! Resistors R8 to R23 (LED series resistors) are not labelled on the board due to space constraints.

The overview of the connectors is provided in Chapter 4.4.4. The correct orientation of the Xiao ESP32-C3 and the motor driver has to be ensured when adding them to the board. For the microcontroller, the orientation of the USB port is indicated on the PCB. For the motor driver, the positions of the two pins, VM and VIn, are labeled on the board. Incorrect orientation of these components can destroy them!

31

## 4. Assembly guide for the remote control and vehicle

Assembling the vehicle and the remote control requires the components from the part lists. As tools, Allen keys with 2 mm and 2.5 mm with a ball head are necessary. Further, small flat pliers and tweezers are needed.
PETG is recommended as a material for 3D printing the components because it is easy to print, suiciently mechanically sturdy, and UV-resistant. Alternatively, PLA or another common filament can be used that oers mechanical stability and stiness. Some parts have to be printed from flexible TPU. These parts are indicated in Chapter 2.3 and carry "TPU" in their name. A print bed with a length of at least 220 mm is required to print all parts. Recommendations for orienting the parts on the print bed and for support are provided in the hints in the printed parts list. A 0.4 mm nozzle and a layer height of 0.2 mm are recommended for all parts. An infill rate of 15 % is suicient.
It should be noted that the printed parts do not oer perfect tolerances. This limitation is due to the type of manufacturing: 3D printing creates imperfect tolerances along specific directions (for example, a layer height of 0.2 mm results in steps of this interval along the Z-direction, meaning edges that are not horizontal or vertical can only be approximated). Further, 3D printing requires support structures for certain geometries to stabilize the part during printing (printing in the air is impossible, but contact with the build plate is required to fabricate structures stably). These support structures partially adhere to the parts, resulting in a poor surface finish. Therefore, printed parts must be fully cleaned of support remnants to ensure a correct fit.
Sometimes, also artifacts occur during 3D printing, like stringing (thin plastic fibers remain between or within parts) or geometric distortions ("elephant foot" or warping: the part warps directly above the print bed due to changes in temperature or air movement during printing). EasyRC components were developed with these issues in mind to minimize these eects as much as possible or to reduce their influence on the function as much as possible. Nonetheless, it may happen that a part does not fit perfectly into its position, rotating elements may rub against their housing, or pockets for screws and nuts may be too tight to allow components to be secured easily.
Therefore, it is essential to be aware of these potential errors during the assembly process. Before securing components with screws, check if a screw can be easily pushed into its recess without significant force. If that is not the case, the hole should be processed with a longer screw by pushing it up and down to remove excess filament, thereby using the screw's threading as a file. Rotating elements should always be tested for ease of movement prior to securing them in place. If a grinding noise occurs, check for plastic strings or imperfections in the surface finish that could cause the friction. Remove excess material carefully with a slotted screwdriver or sandpaper. The advantage of 3D printed parts is their low cost and fast manufacturing (for small batch manufacturing). If a component is defective, it can be reprinted within a few hours, allowing for a quick replacement of broken parts.
EasyRC components are assembled using metric screws and hex nuts. Hex nuts are used as thread inserts because delicate printed threads are unstable and cannot be reused multiple times before they are ground down or pulled out of the part. Alternatively, parts could be fused with cyanoacrylate adhesive (superglue), but this process does not allow them to be disassembled without destroying them. However, superglue or hot glue is a fast means to repair broken components.

32

Securing components with screws requires placing the hex nuts in their pockets correctly. Placing them by hand is not always possible, depending on the position of the nut within a part and also on the tolerances of the parts. To this end, the nut can be screwed onto a screw and then placed in its recess, using the screw to push it into position at the correct angle. Alternatively, the nut can be placed loosely above or within its pocket, and a screw can be approached from the opposing side to pull the nut into its recess. These two processes are depicted in the following figure.

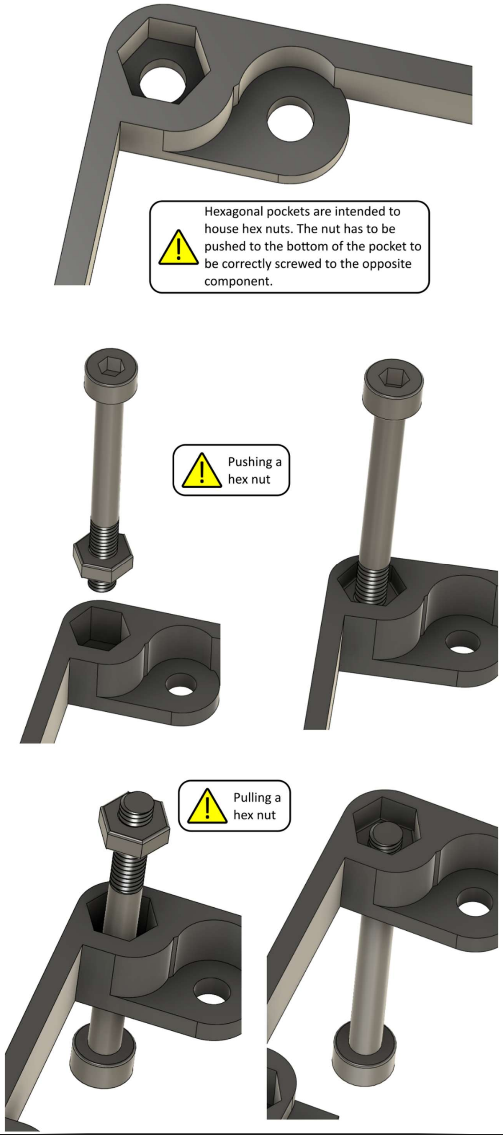
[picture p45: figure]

33

34

Here is a guide to help you easily find the correct screw lengths. If this page is printed precisely on A4 paper, the screw lengths match exactly those shown in the size chart.

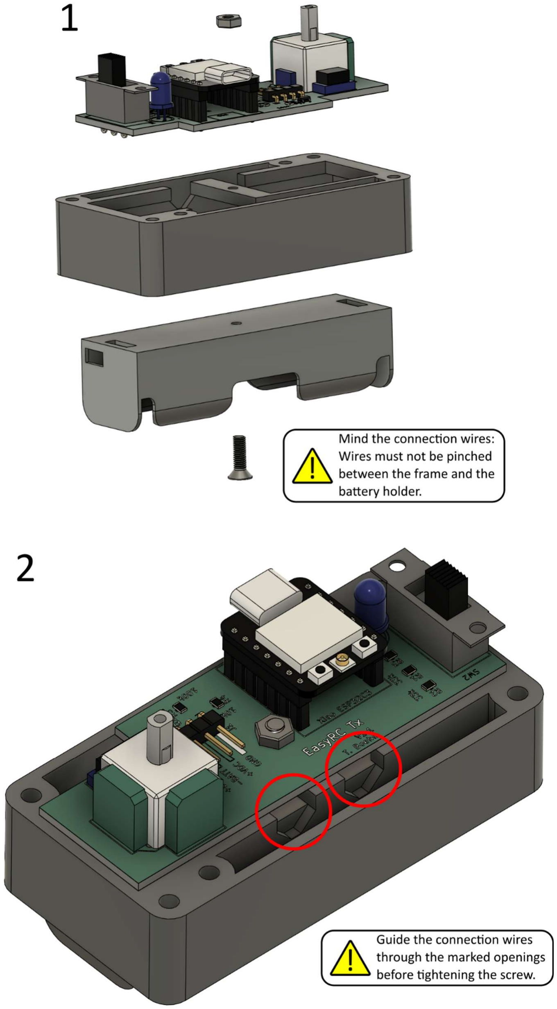
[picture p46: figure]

35

### 4.1 Remote control

### 4.1.1 Installation of PCB and battery holder

Required parts: Remote control lower intermediate frame, EasyRC Tx circuit board, battery holder 1x 18650 LiIon cell, M3x10 mm countersunk screw, M3 hex nut

36

Connections: The battery holder must be connected to (1); the red wire needs to be connected to +BATT and the black wire to -BATT. The wires from the microcontroller must be connected to (2); the red wire needs to be plugged into +VDC, and the black wire into GND.
Attention: The battery connector (1) is reverse polarity protected; however, the microcontroller is not. If (2) is connected incorrectly, the microcontroller is instantly destroyed as soon as the remote control is switched on!

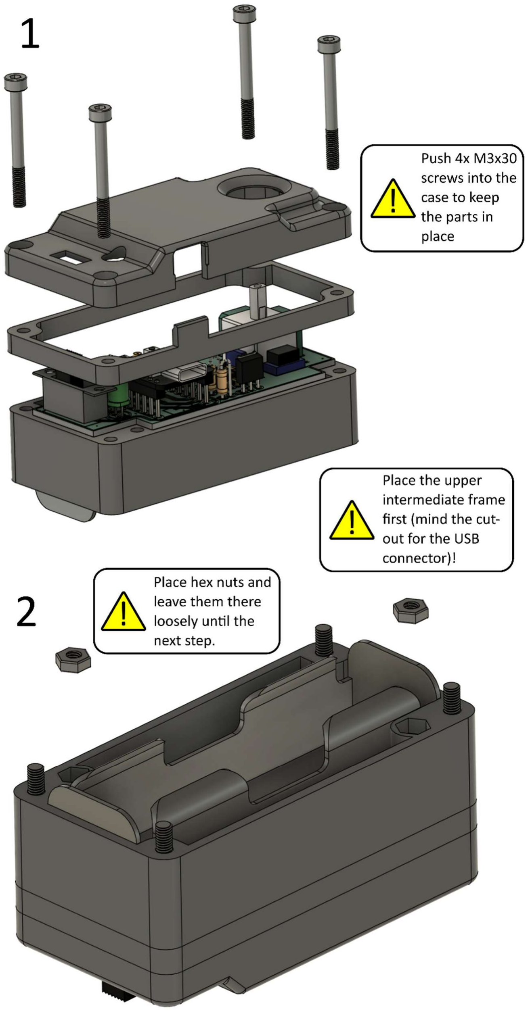
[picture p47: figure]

37

### 4.1.2 Fastening top and bottom

Required parts: Remote control (prepared), Remote control top, Remote control upper intermediate frame, Remote control bottom, M3x30 mm screw (4x), M3 hex nut (6x)

38

39

### 4.1.3 Completion remote control

Required parts: Remote control (prepared), Remote control joystick extension, Remote control battery cover, M3x8 mm Schraube (2x)

40

### 4.1.4 Overview remote control

Number | Designation | Explanation
1 | Joystick | Joystick used to control the vehicle (forward/reverse/left/right). Pushing the joystick activates the vehicle's horn.
2 | On/o switch | Left position: o; right position: on
3 | USB connector | USB connector type C
4 | Status LED | The LED is permanently on while the remote control is switched on. It blinks twice per second if the battery is low.

41

### 4.2 Drive train and wheels

### 4.2.1 Motor preparation

Required parts: geared DC motor, 25 teeth gear

42

### 4.2.2 Intermediate gear

Required parts: 16 teeth gear, 16 teeth gear bearing mount (2x), ball bearing 605 (5x14x5 mm, 2x), M3x30 mm screw, M3 nex nut

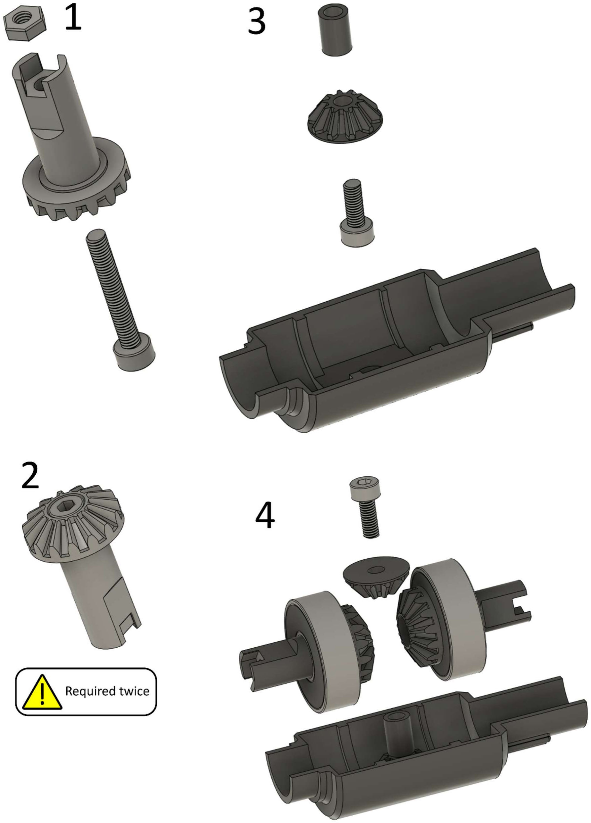
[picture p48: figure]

43

### 4.2.3 Dierential

Required parts: Dierential case (2x), 10 teeth crown gear (2x), dierential spacer, 15 teeth crown gear (2x), 24 teeth gear, dierential spacer ring, ball bearing 608 (8x22x7 mm, 2x), ball bearing 6802 (15x24x5 mm, 2x), M3x8 mm screw (2x), M3x20 mm screw (2x), M3 hex nut (2x)

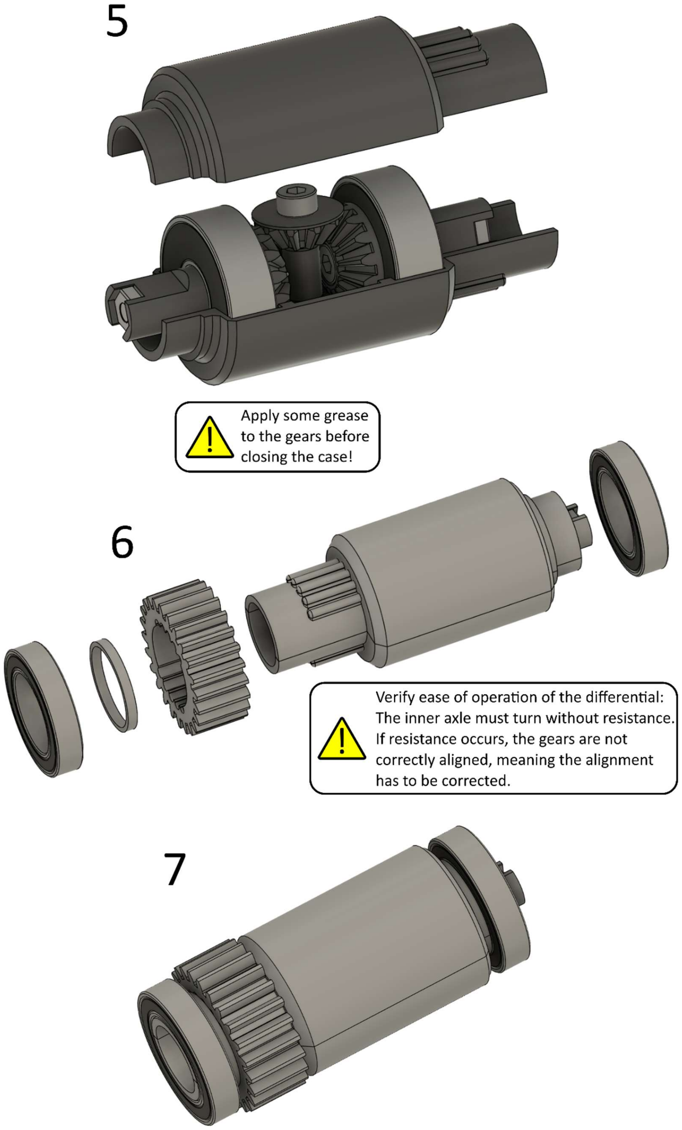
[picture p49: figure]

44

45

### Did you know?

A dierential is installed in every car. It is necessary to enable dierent wheel speeds at a driven axle, which is crucial for cornering. In a turn, the inner wheel must rotate more slowly than the outer wheel to maintain traction on both wheels. Vehicles with front-wheel drive or rear-wheel drive only need one dierential between the left and right driven wheels. Cars with all-wheel drive even require three dierentials (in the front and rear between the left and right wheels, as well as a center dierential between the front and rear axles).
The disadvantage of a dierential becomes apparent when one wheel loses traction. In this case, the wheel can spin freely while the other wheel remains stationary – the car is stuck. This issue does not apply to on-road cars, as this problem virtually never occurs. However, it is a common problem for o-road vehicles. Then, special dierentials that are self-locking are employed, or manually operated dierential locks are available. They turn o the dierential function so that both wheels rotate at the same speed. Notably, dierential locks must only be engaged in o-road use to prevent additional tire wear, poorer traction during cornering, and unnecessarily high strain on the power train when driving on-road.

46

### 4.2.4 Rear wheels

Required parts: Rear rim (2x), Tire (2x), Rear rim spacer (2x), Left rear axle, Right rear axle, ball bearing 608 (8x22x7 mm, 2x), M3x30 mm screw (2x), M3 hex nut (2x)

47

### 4.2.5 Connection of the drive train and chassis

Required parts: Rear wheels, Dierential, Intermediate gear, Motor with gear (all already prepared), Chassis bottom, Chassis top, M3x30 mm screw (8x), M3 hex nut (14x)

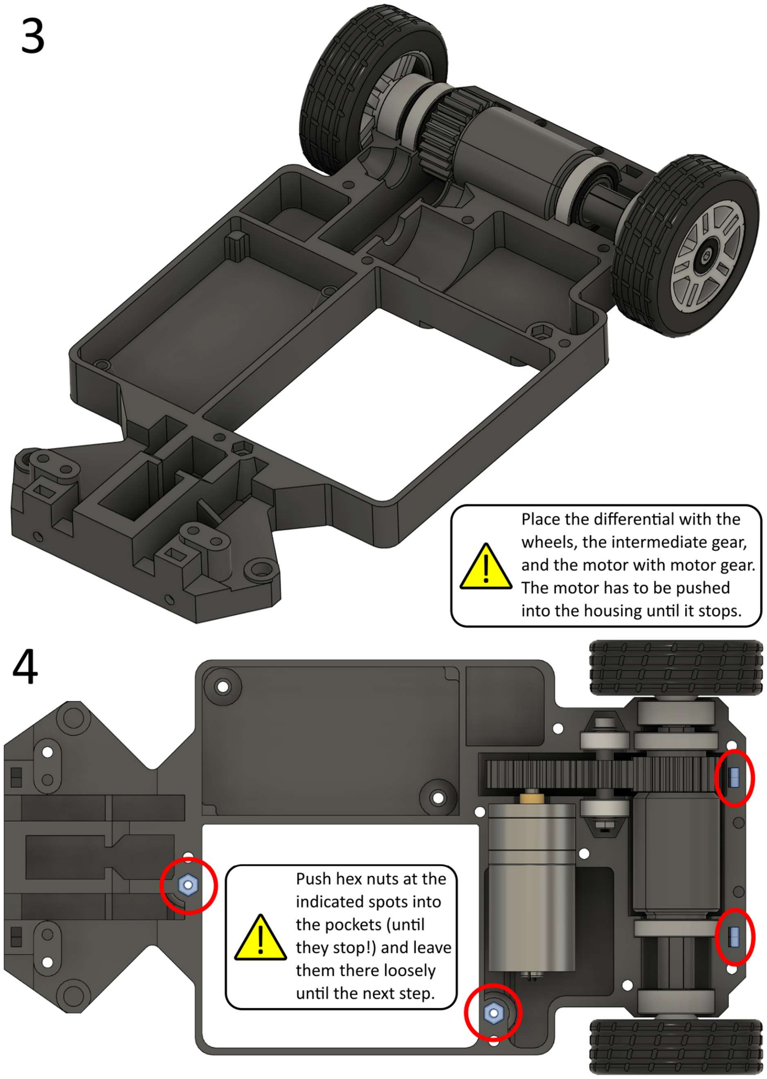
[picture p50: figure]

48

49

50

### Did you know?

Gearboxes are ubiquitous: Not only cars, but also every power drill, mechanical clocks, and even salad spinners include gearboxes. A gearbox reduces or increases the speed of a mechanical drive. In return, the torque (force) becomes more or less because the power of a mechanical drive is the product of torque x speed. Ideal gearboxes have very small friction losses, meaning their eiciency is typically >90%. Hence, the output of a motor with a 1:10 transmission spins ten times slower but is almost ten times stronger. The transmission is a result of the ratio between the tooth count of the gear pair.
The EasyRC vehicle utilizes a motor with an integrated gearbox because the desired 1:10 transmission ratio can only be achieved with printed parts using a multistage gearbox, which requires a significant amount of space and increases the risk of failure. The printed gearbox in the vehicle (25:24 transmission, almost 1:1) is only used to create suicient space for the dierential between the motor and the driven axle. The tooth count of the intermediate gear (idler gear) does not play a role: The transmission ratio is only dependent on the input and output shaft.

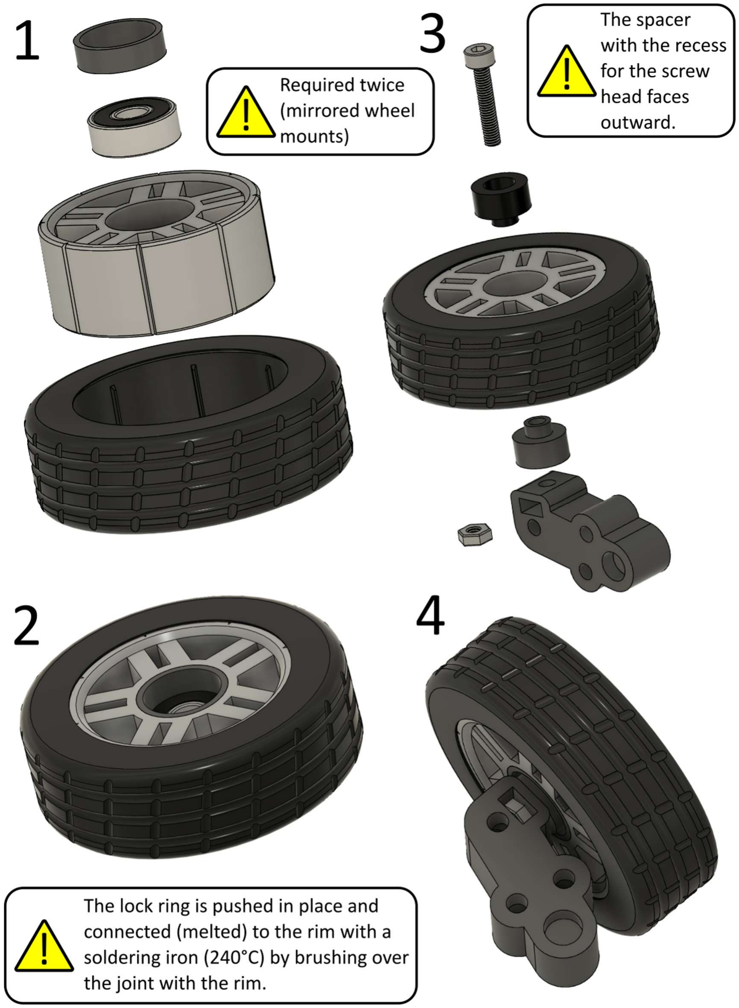
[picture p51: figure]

51

### 4.3 Front wheels and steering

### 4.3.1 Preparation of front wheels

Required parts: Front rim (2x), Tire (2x), Front rim locking ring (2x), Front rim spacer (2x), Front wheel mount (2x, mirrored versions), Front wheel mount spacer (2x), ball bearing 605 (5x14x5 mm, 2x), M3x16 mm screw (2x), M3 hex nut (2x)

52

### 4.3.2 Steering linkage

Required parts: Front wheels (prepared), Steering linkage, Steering linkage connector (2x), M3x16 mm screw (2x), M3x20 mm screw (4x), M3 hex nut (4x)

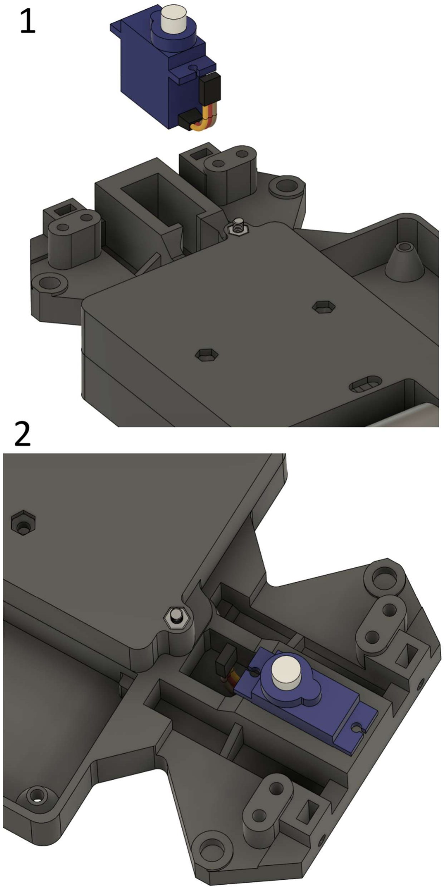
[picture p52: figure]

53

### 4.3.3 Connection of the front wheels and chassis

Required parts: Chassis (prepared), Front wheels with steering linkage (prepared), Chassis securing bracket, MG90S servo motor, M3x20 mm screw (2x), M3x30 mm screw (2x), M3 hex nut (4x)

54

55

56

### Did you know?

The inner wheel moves a little further than the outer wheel when the steering wheel is rotated during a turn: The steering angle of the inner wheel is larger than that of the outer wheel. This arrangement is referred to as Ackermann steering geometry and supports vehicle traction in tight turns. Since only the front wheels are actively steered in cars, a car has to travel on a circle whose center is an extension of the rear axle to prevent the wheels from slipping. Front wheel steering is also the reason why parking in narrow parking lots is easier in reverse than when driving forward: The turning point of the car is always located at the rear axle.
If the front wheels use the exact same steering angle in this constellation, their angles do not meet at this turning point. Consequently, they cannot move in a stable circle but are pulled sideways relative to their direction of travel. The Ackermann steering geometry approaches both front wheels to this ideal turning point, allowing the car to corner as stably as possible. This concept was originally developed for horse-drawn carriages and later adapted for cars. However, cars often do not employ full Ackermann steering geometry because this setup predominantly increases traction at low speeds. Fast cornering results in various other eects, such as shifting the car's mass to the outer wheels and body roll toward the outer side of the turn, meaning that other steering geometries work better.
F1 cars represent the extreme case: they even use anti-Ackermann steering geometry, meaning the outer wheel has a larger steering angle than the inner wheel to maintain a high tire temperature due to the additional friction (higher slip angle) of the inner wheel. High-speed applications require high tire temperatures to ensure optimal traction. The disadvantages of this configuration are elevated tire wear and poorer turning characteristics at slow speeds, which are not significant concerns for these racing cars.

57

58

### 4.4 Finalization of the chassis

### 4.4.1 Printed circuit board

Required parts: Chassis (prepared), EasyRC Rx circuit board, M3x16 mm screw (2x), M3 hex nut (2x)

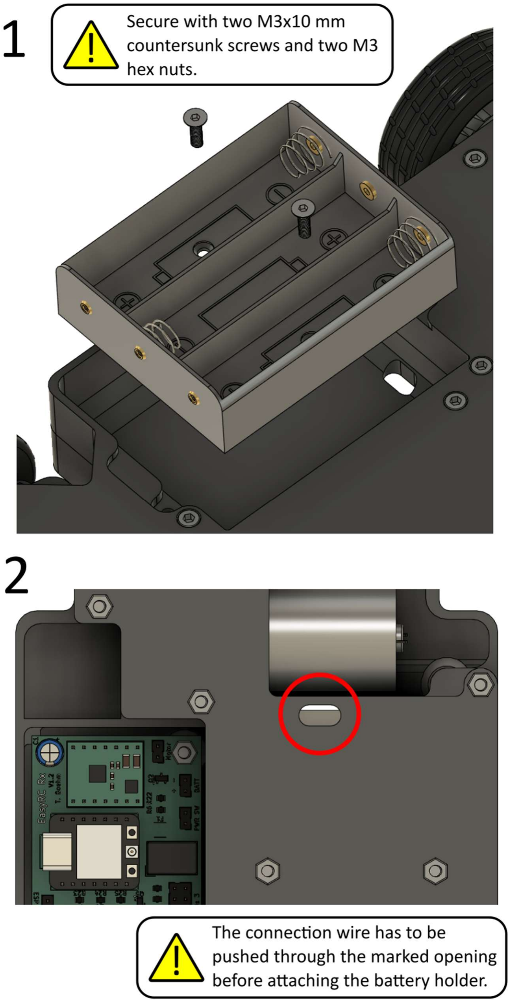
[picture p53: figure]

59

### 4.4.2 Battery compartment

Required parts: Chassis (prepared), Battery lid, Battery holder 3x 18650 LiIon cell, M3x16 mm screw (2x), M3x10 mm countersunk screw (2x), M3 hex nut (2x)

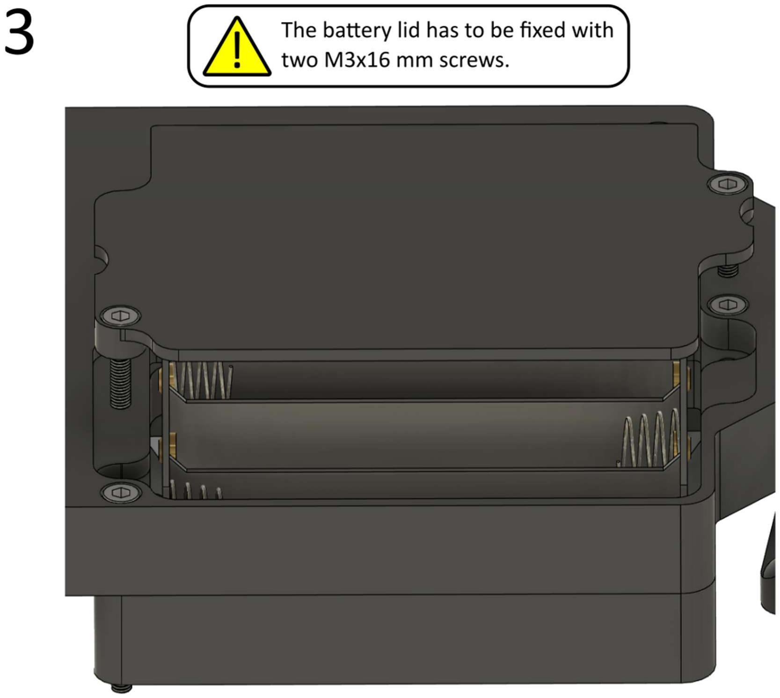
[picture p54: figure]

60

61

### 4.4.3 Bumpers

Required parts: Chassis (prepared), Front bumper, Rear bumper, on/o switch, M3x8 mm screw (4x), M3 hex nut (2x)

62

63

### 4.4.4 Wiring

The wires that connect to the chassis encompass the numbers 1 to 4: Battery holder, on/o switch, drive motor, and steering servo can already be connected. Ensure the polarity is correct (refer to the table below).
The LEDs (labels 5 to 8) will be connected during the final assembly of the car, as described in Chapter 7.3. Four LEDs can be connected per channel. The standard body kit is designed for two LEDs per channel. Any of the four connectors per channel can be used to connect an LED (without preferential order).
Number | Designation | Polarity
1 | BATT (battery connection) | Red to +; black to -
2 | PWR SW (on/o switch) | No matter
3 | Motor (drive motor) | No matter (rotation direction set by software)
4 | Servo (steering servo) | Yellow to data; red to 5V; brown to GND
5 | LEDs 0 (headlights)* | Red to +; black to -
6 | LEDs 1 (rear lights)* | Red to +; black to -
7 | LEDs 2 (left indicator lights)* | Red to +; black to -
8 | LEDs 3 (right indicator lights)* | Red to +; black to -
*The LED connector headers consist of four connector pairs: Up to four LEDs can be connected per channel. In this view, the upper contacts are + and the lower contacts are -. The body kit is designed for two LEDs per channel.


64

### 4.4.5 Preparation of the servo horn

Required parts: Servo horn attachment, servo horn, M3x16 mm screw, M3 hex nut

There are two 3D models for the servo horn attachment because the MG90 servos come with servo horns of dierent sizes. The smaller servo horn has a length of approximately 32 mm, and the larger one has a length of approximately 37 mm. The servo horn attachment with the suitable recess must be printed and employed to enable steering without backlash.

65

### 4.5 Body kit

### 4.5.1 Rear wing

Required parts: Rear body, Rear wing, Rear wing holder, M3x8 mm screw (2x), M3x16 mm screw (2x), M3 hex nut (2x)


66

67

### 4.5.2 Body connection and windows

Required parts: Rear body (prepared), Front body, Windows (1x front, 1x left front, 1x left rear, 1x right front, 1x right rear, 1x rear), Window holder, M3x8 mm screw (15x), M3 hex nut (15x)


68

69

### 4.5.3 Headlights

Required parts: Body (prepared), Front light clamp, Front LED insert (2x), LED white (2x), LED yellow (2x), M3x8 mm screw (2x), M3 hex nut (2x)

70

71
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

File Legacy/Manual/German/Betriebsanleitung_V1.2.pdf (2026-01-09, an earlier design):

# EasyRC – Open Source Fernsteuerungsplattform

## Betriebsanleitung

Version 1.2; Stand: 09.01.2026

2

## Inhaltsverzeichnis

1. Hinweise und Spezifikationen | 4
1.1 | Sicherheitshinweise | 4
1.2 | Spezifikationen der EasyRC-Plattform | 5
2. Teilelisten | 6
2.1 | Elektronikbauteile | 6
2.2 | Metallbauteile | 8
2.3 | Gedruckte Bauteile | 9
3. Elektronik | 16
3.1 | Einführung in die Elektronik | 16
3.2 | Fertigung und Bestückung der Leiterplatten | 17
3.3 | Crimpen und Verlöten der Elektronikbauteile | 18
3.4 | Komponentenliste | 19
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

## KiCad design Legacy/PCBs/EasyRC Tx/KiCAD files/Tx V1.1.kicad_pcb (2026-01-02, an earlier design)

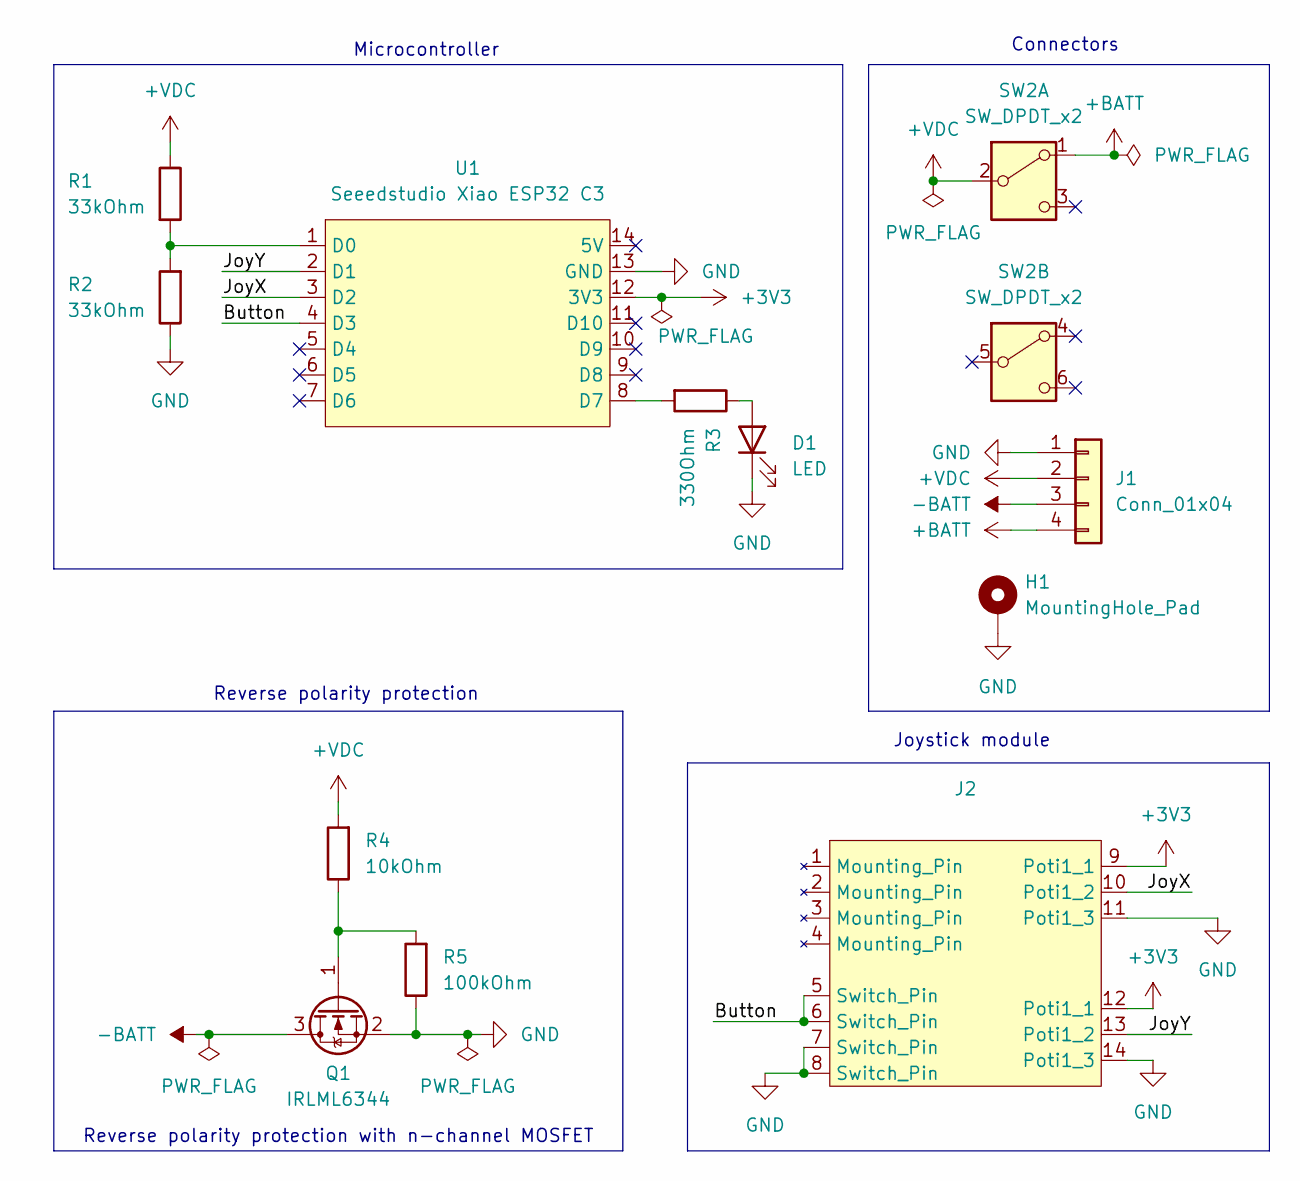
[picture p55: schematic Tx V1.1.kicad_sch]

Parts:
D1: LED; LED_D5.0mm
H1: MountingHole_Pad; MountingHole_3.2mm_M3_DIN965_Pad_TopBottom
J1: Conn_01x04; PinHeader_1x04_P2.54mm_Horizontal
J2: PS5 Joystick
Q1: IRLML6344; SOT-23
R1, R2: 33kOhm; R_0805_2012Metric_Pad1.20x1.40mm_HandSolder
R3: 330Ohm; R_0805_2012Metric_Pad1.20x1.40mm_HandSolder
R4: 10kOhm; R_0805_2012Metric_Pad1.20x1.40mm_HandSolder
R5: 100kOhm; R_0805_2012Metric_Pad1.20x1.40mm_HandSolder
SW2: SW_DPDT_x2; Wentronic S166 slide switch
U1: Seeedstudio Xiao ESP32 C3; Xiao ESP32C3

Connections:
+3V3: J2.9 (Poti1_1), J2.12 (Poti1_1), U1.12 (3V3)
+BATT: J1.4, SW2.1 (A)
+VDC: J1.2, R1.1, R4.2, SW2.2 (B)
-BATT: J1.3, Q1.3 (D)
/Button: J2.5 (Switch_Pin), J2.6 (Switch_Pin), U1.4 (D3)
/JoyX: J2.10 (Poti1_2), U1.3 (D2)
/JoyY: J2.13 (Poti1_2), U1.2 (D1)
GND: D1.1 (K), H1.1, J1.1, J2.7 (Switch_Pin), J2.8 (Switch_Pin), J2.11 (Poti1_3), J2.14 (Poti1_3), Q1.2 (S), R2.1, R5.1, U1.13 (GND)
unnamed: D1.2 (A), R3.1
unnamed: Q1.1 (G), R4.1, R5.2
unnamed: R1.2, R2.2, U1.1 (D0)
unnamed: R3.2, U1.8 (D7)

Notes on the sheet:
Reverse polarity protection
Joystick module
Connectors
Microcontroller
Reverse polarity protection with n-channel MOSFET

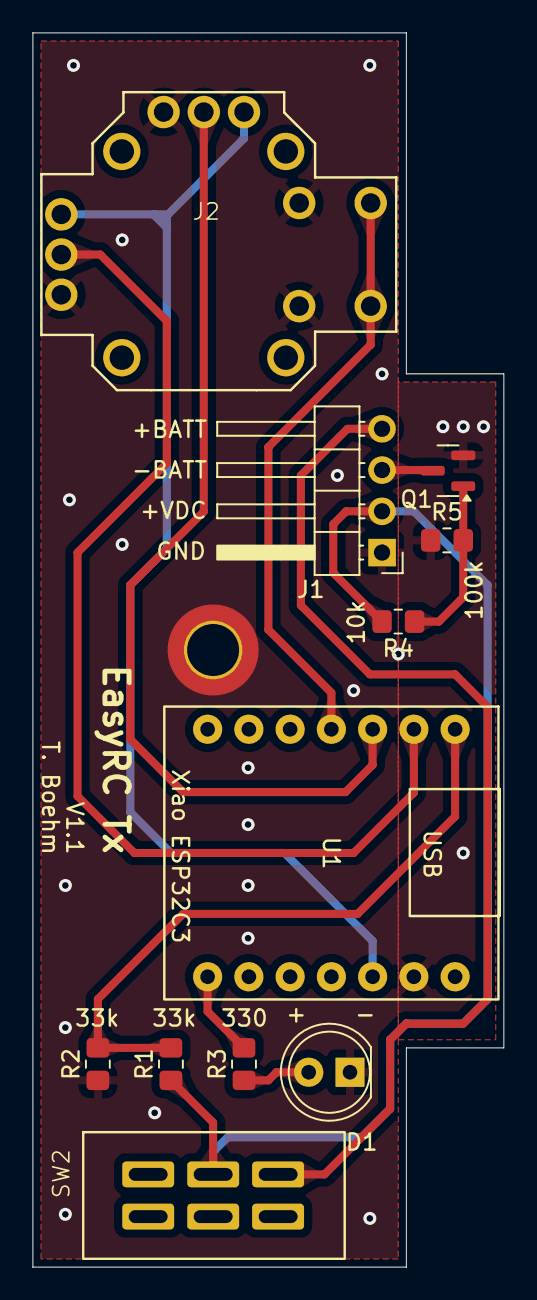
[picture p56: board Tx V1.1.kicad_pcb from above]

Board: 2 copper layers, 29.0 x 76.0 mm, 12 parts (0 on the bottom side), 12 nets.

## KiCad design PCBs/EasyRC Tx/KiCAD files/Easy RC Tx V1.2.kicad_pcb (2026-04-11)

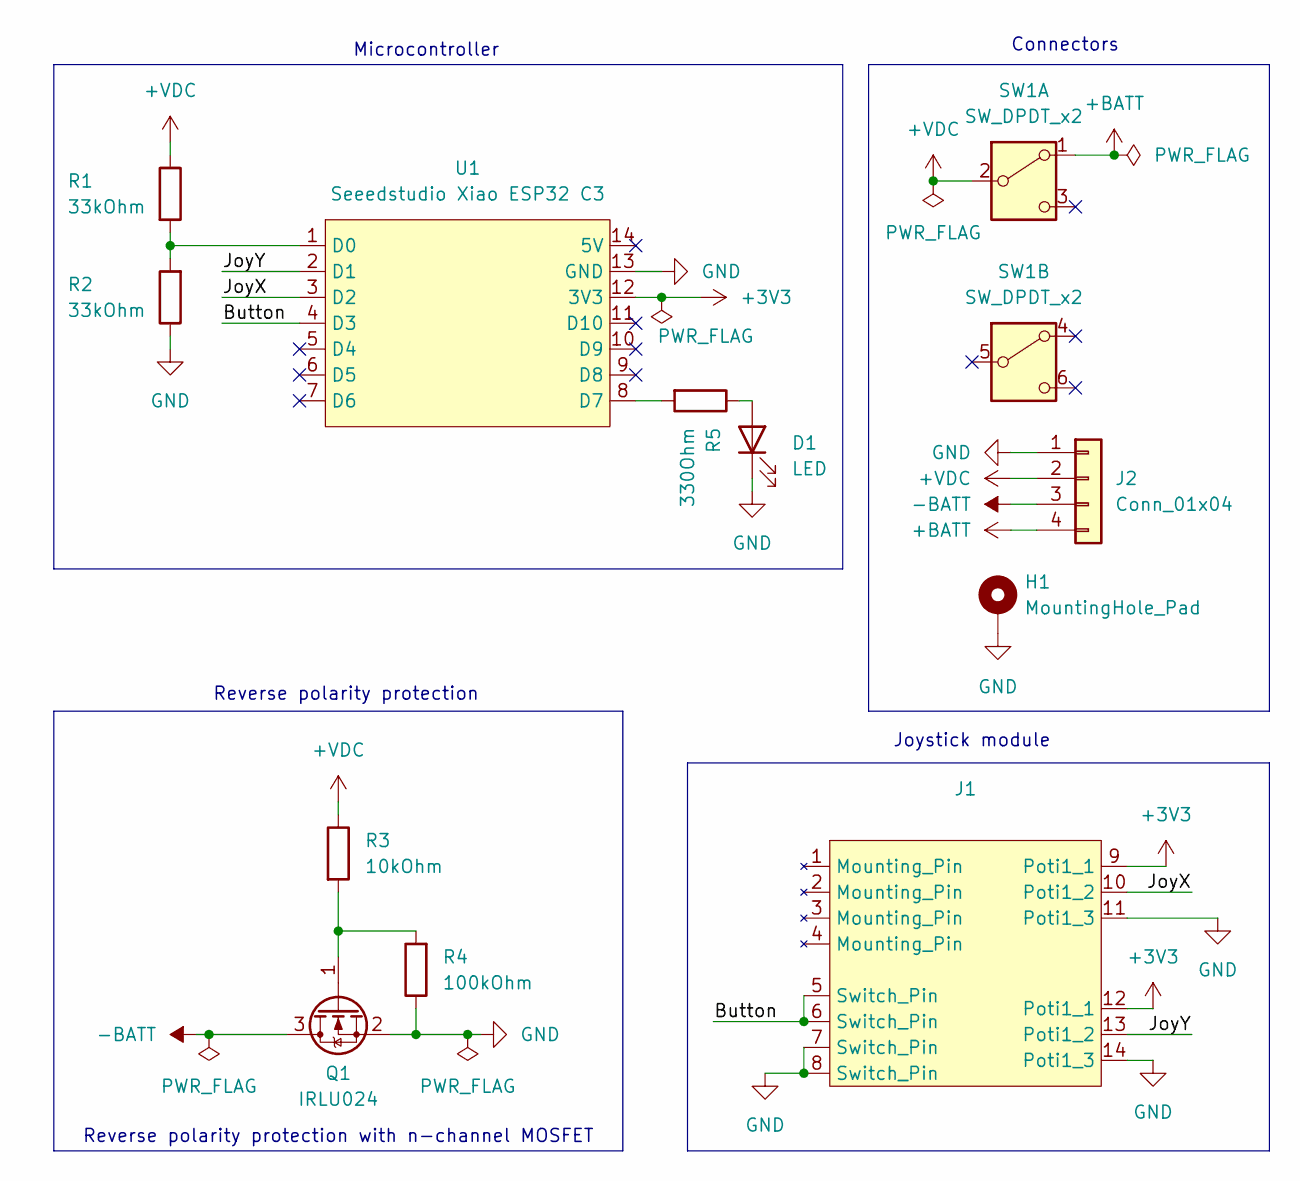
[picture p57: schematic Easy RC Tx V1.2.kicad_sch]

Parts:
D1: LED; LED_D5.0mm
H1: MountingHole_Pad; MountingHole_3.2mm_M3_DIN965_Pad_TopBottom
J1: PS5 Joystick
J2: Conn_01x04; PinHeader_1x04_P2.54mm_Horizontal
Q1: IRLU024; TO-251-3_Vertical
R1, R2: 33kOhm; R_Axial_DIN0207_L6.3mm_D2.5mm_P2.54mm_Vertical
R3: 10kOhm; R_Axial_DIN0207_L6.3mm_D2.5mm_P2.54mm_Vertical
R4: 100kOhm; R_Axial_DIN0207_L6.3mm_D2.5mm_P2.54mm_Vertical
R5: 330Ohm; R_Axial_DIN0207_L6.3mm_D2.5mm_P2.54mm_Vertical
SW1: SW_DPDT_x2; Wentronic S166 slide switch
U1: Seeedstudio Xiao ESP32 C3; Xiao ESP32C3

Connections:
+3V3: J1.9 (Poti1_1), J1.12 (Poti1_1), U1.12 (3V3)
+BATT: J2.4, SW1.1 (A)
+VDC: J2.2, R1.1, R3.1, SW1.2 (B)
-BATT: J2.3, Q1.3 (D)
/Button: J1.5 (Switch_Pin), J1.6 (Switch_Pin), U1.4 (D3)
/JoyX: J1.10 (Poti1_2), U1.3 (D2)
/JoyY: J1.13 (Poti1_2), U1.2 (D1)
GND: D1.1 (K), H1.1, J1.7 (Switch_Pin), J1.8 (Switch_Pin), J1.11 (Poti1_3), J1.14 (Poti1_3), J2.1, Q1.2 (S), R2.1, R4.1, U1.13 (GND)
unnamed: D1.2 (A), R5.1
unnamed: Q1.1 (G), R3.2, R4.2
unnamed: R1.2, R2.2, U1.1 (D0)
unnamed: R5.2, U1.8 (D7)

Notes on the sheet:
Reverse polarity protection
Joystick module
Connectors
Microcontroller
Reverse polarity protection with n-channel MOSFET

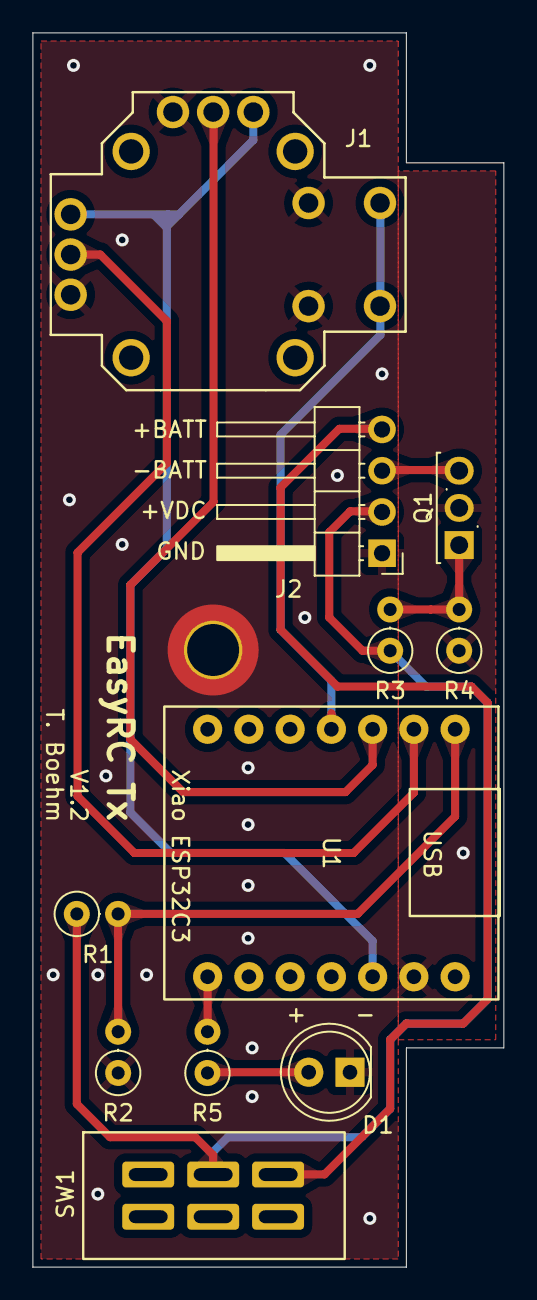
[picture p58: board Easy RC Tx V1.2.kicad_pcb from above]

Board: 2 copper layers, 29.0 x 76.0 mm, 12 parts (0 on the bottom side), 12 nets.

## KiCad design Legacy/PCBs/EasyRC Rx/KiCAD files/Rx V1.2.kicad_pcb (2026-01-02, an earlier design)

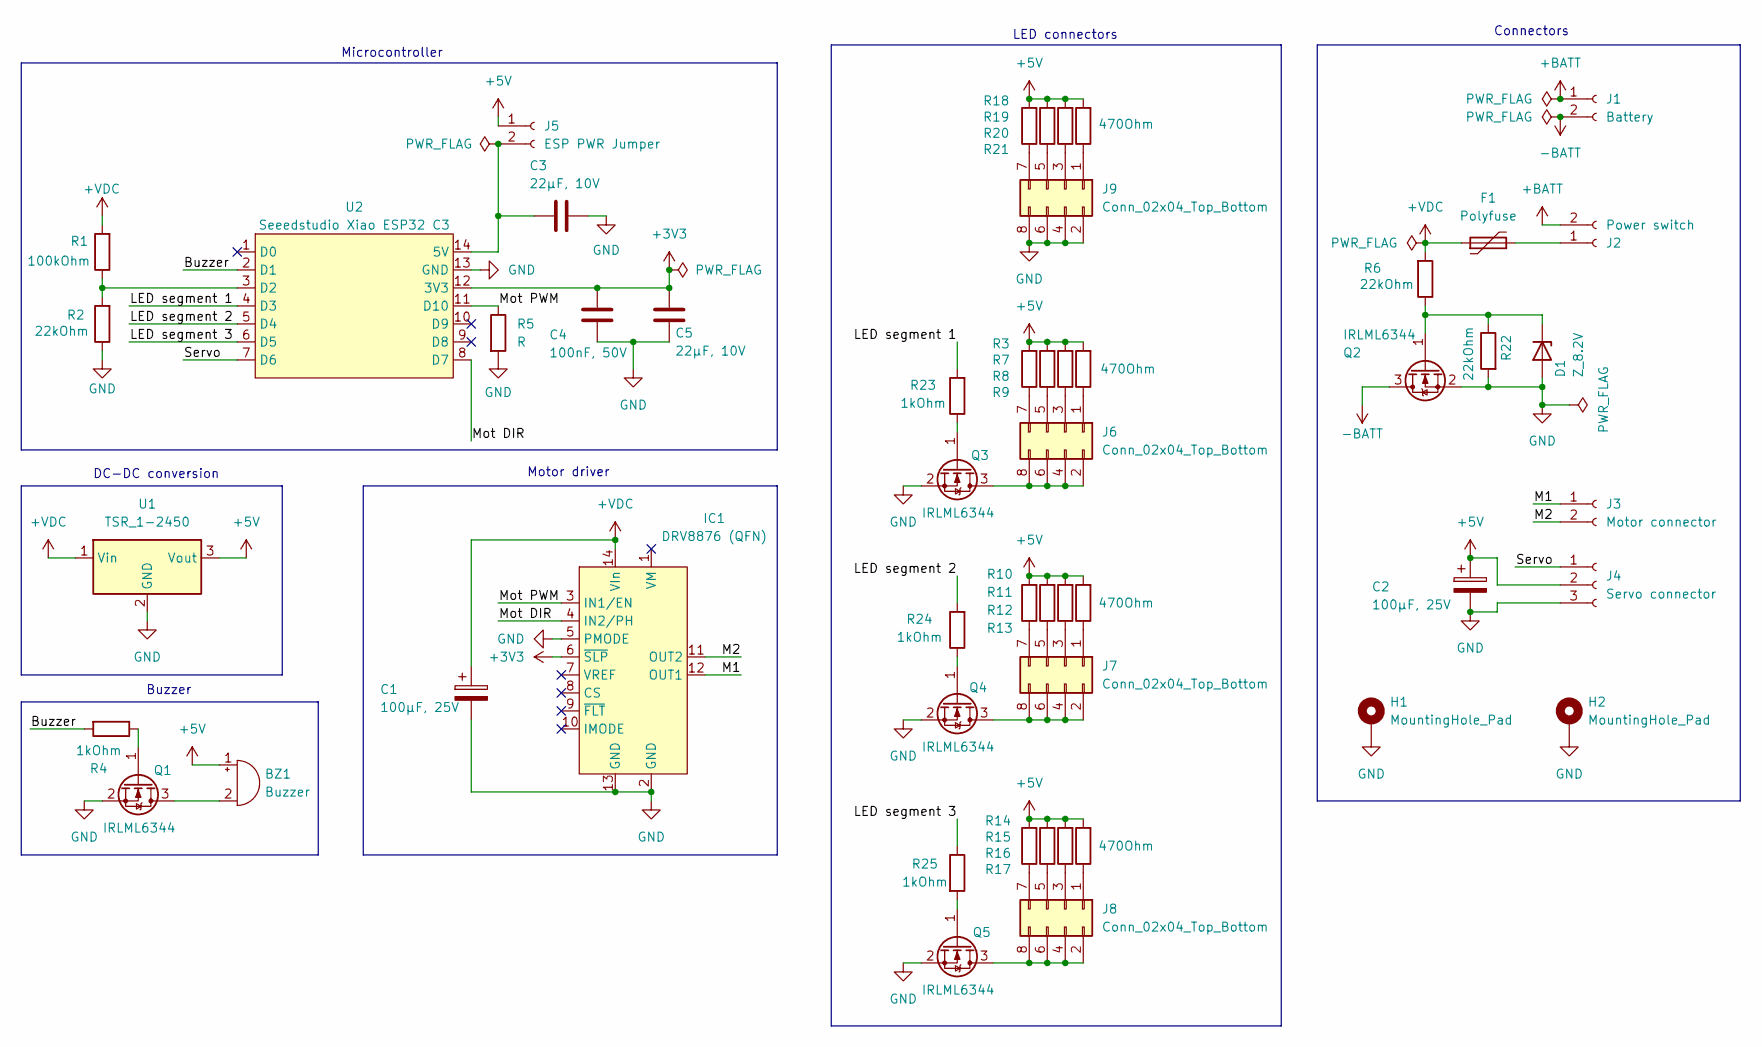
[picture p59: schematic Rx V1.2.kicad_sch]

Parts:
BZ1: Buzzer; Buzzer 12mm 6.5mm spacing
C1, C2: 100µF, 25V; CP_Radial_D6.3mm_P2.50mm
C3, C5: 22µF, 10V; C_1206_3216Metric_Pad1.33x1.80mm_HandSolder
C4: 100nF, 50V; C_0805_2012Metric_Pad1.18x1.45mm_HandSolder
D1: Z_8.2V; SOT-23_Handsoldering
F1: Polyfuse; Fuse_1812_4532Metric_Pad1.30x3.40mm_HandSolder
H1, H2: MountingHole_Pad; MountingHole_3.2mm_M3_DIN965_Pad_TopBottom
IC1: DRV8876 (QFN); DRV8876(QFN)
J1: Battery; PinHeader_1x02_P2.54mm_Vertical
J2: Power switch; PinHeader_1x02_P2.54mm_Vertical
J3: Motor connector; PinHeader_1x02_P2.54mm_Vertical
J4: Servo connector; PinHeader_1x03_P2.54mm_Vertical
J5: ESP PWR Jumper; PinHeader_1x02_P2.54mm_Vertical
J6, J7, J8, J9: Conn_02x04_Top_Bottom; PinHeader_2x04_P2.54mm_Vertical
Q1, Q2, Q3, Q4, Q5: IRLML6344; SOT-23
R1: 100kOhm; R_0805_2012Metric_Pad1.20x1.40mm_HandSolder
R2, R6, R22: 22kOhm; R_0805_2012Metric_Pad1.20x1.40mm_HandSolder
R3, R7, R8, R9, R10, R11, R12, R13, R14, R15, R16, R17, R18, R19, R20, R21: 470Ohm; R_0805_2012Metric_Pad1.20x1.40mm_HandSolder
R4, R23, R24, R25: 1kOhm; R_0805_2012Metric_Pad1.20x1.40mm_HandSolder
R5: R; R_0805_2012Metric_Pad1.20x1.40mm_HandSolder
U1: TSR_1-2450; Converter_DCDC_TRACO_TSR-1_THT
U2: Seeedstudio Xiao ESP32 C3; Xiao ESP32C3

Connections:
+3V3: C4.1, C5.1, IC1.6 (~SLP), U2.12 (3V3)
+5V: BZ1.1 (+), C2.1, J4.2, J5.1, R3.2, R7.2, R8.2, R9.2, R10.2, R11.2, R12.2, R13.2, R14.2, R15.2, R16.2, R17.2, R18.2, R19.2, R20.2, R21.2, U1.3 (Vout)
+BATT: J1.1, J2.2
+VDC: C1.1, F1.1, IC1.14 (VIn), R1.2, R6.2, U1.1 (Vin)
-BATT: J1.2, Q2.3 (D)
/Buzzer: R4.2, U2.2 (D1)
/LED segment 1: R23.2, U2.4 (D3)
/LED segment 2: R24.2, U2.5 (D4)
/LED segment 3: R25.1, U2.6 (D5)
/M1: IC1.12 (OUT1), J3.1
/M2: IC1.11 (OUT2), J3.2
/Mot DIR: IC1.4 (IN2/PH), U2.8 (D7)
/Mot PWM: IC1.3 (IN1/EN), R5.1, U2.11 (D10)
/Servo: J4.1, U2.7 (D6)
GND: C1.2, C2.2, C3.2, C4.2, C5.2, D1.1 (A), H1.1, H2.1, IC1.2 (GND), IC1.5 (PMODE), IC1.13 (GND), J4.3, J9.2, J9.4, J9.6, J9.8, Q1.2 (S), Q2.2 (S), Q3.2 (S), Q4.2 (S), Q5.2 (S), R2.1, R5.2, R22.2, U1.2 (GND), U2.13 (GND)
unnamed: BZ1.2 (-), Q1.3 (D)
unnamed: D1.3 (K), Q2.1 (G), R6.1, R22.1
unnamed: F1.2, J2.1
unnamed: C3.1, J5.2, U2.14 (5V)
unnamed: J6.1, R9.1
unnamed: J6.2, J6.4, J6.6, J6.8, Q3.3 (D)
unnamed: J6.3, R8.1
unnamed: J6.5, R7.1
unnamed: J6.7, R3.1
unnamed: J7.1, R13.1
unnamed: J7.2, J7.4, J7.6, J7.8, Q4.3 (D)
unnamed: J7.3, R12.1
unnamed: J7.5, R11.1
unnamed: J7.7, R10.1
unnamed: J8.1, R17.1
unnamed: J8.2, J8.4, J8.6, J8.8, Q5.3 (D)
unnamed: J8.3, R16.1
unnamed: J8.5, R15.1
unnamed: J8.7, R14.1
unnamed: J9.1, R21.1
unnamed: J9.3, R20.1
unnamed: J9.5, R19.1
unnamed: J9.7, R18.1
unnamed: Q1.1 (G), R4.1
unnamed: Q3.1 (G), R23.1
unnamed: Q4.1 (G), R24.1
unnamed: Q5.1 (G), R25.2
unnamed: R1.1, R2.2, U2.3 (D2)

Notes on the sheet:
Buzzer
Microcontroller
LED connectors
DC-DC conversion
Connectors
Motor driver

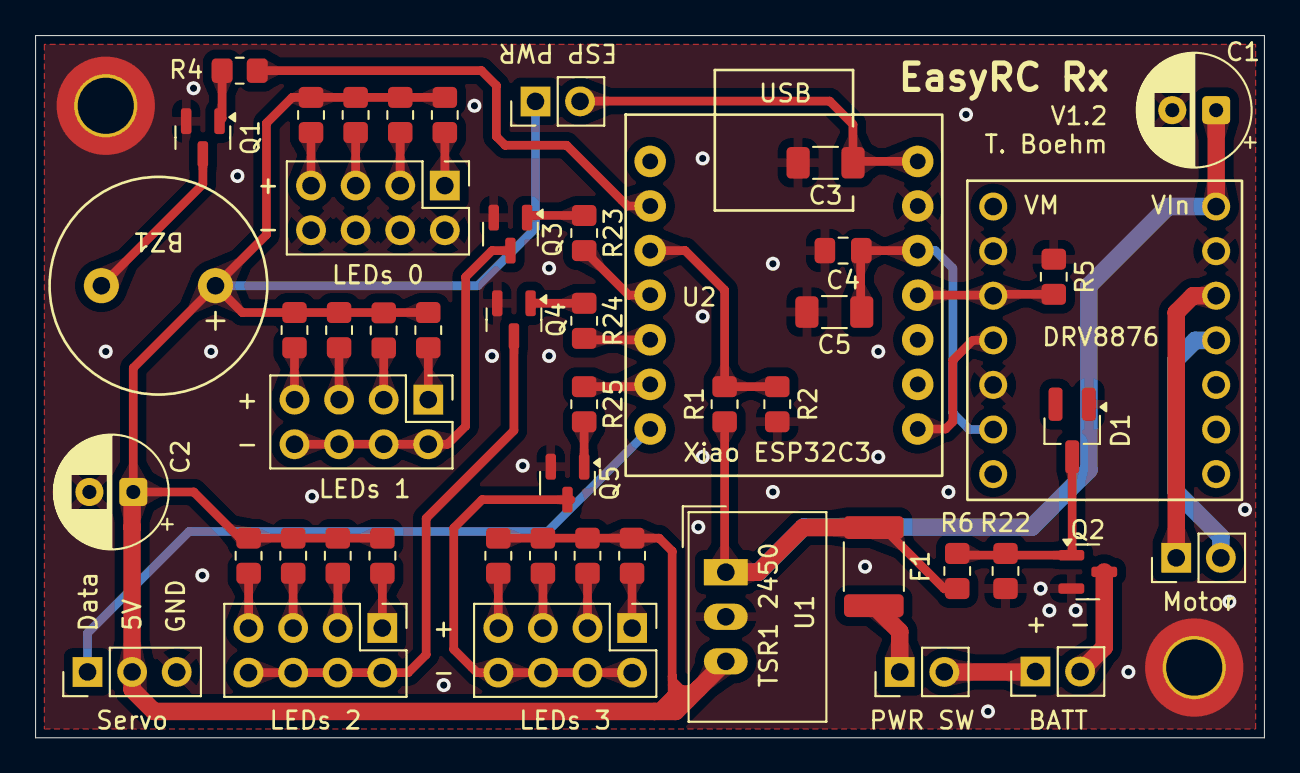
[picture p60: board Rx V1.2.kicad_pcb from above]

Board: 2 copper layers, 70.0 x 40.0 mm, 52 parts (0 on the bottom side), 43 nets.

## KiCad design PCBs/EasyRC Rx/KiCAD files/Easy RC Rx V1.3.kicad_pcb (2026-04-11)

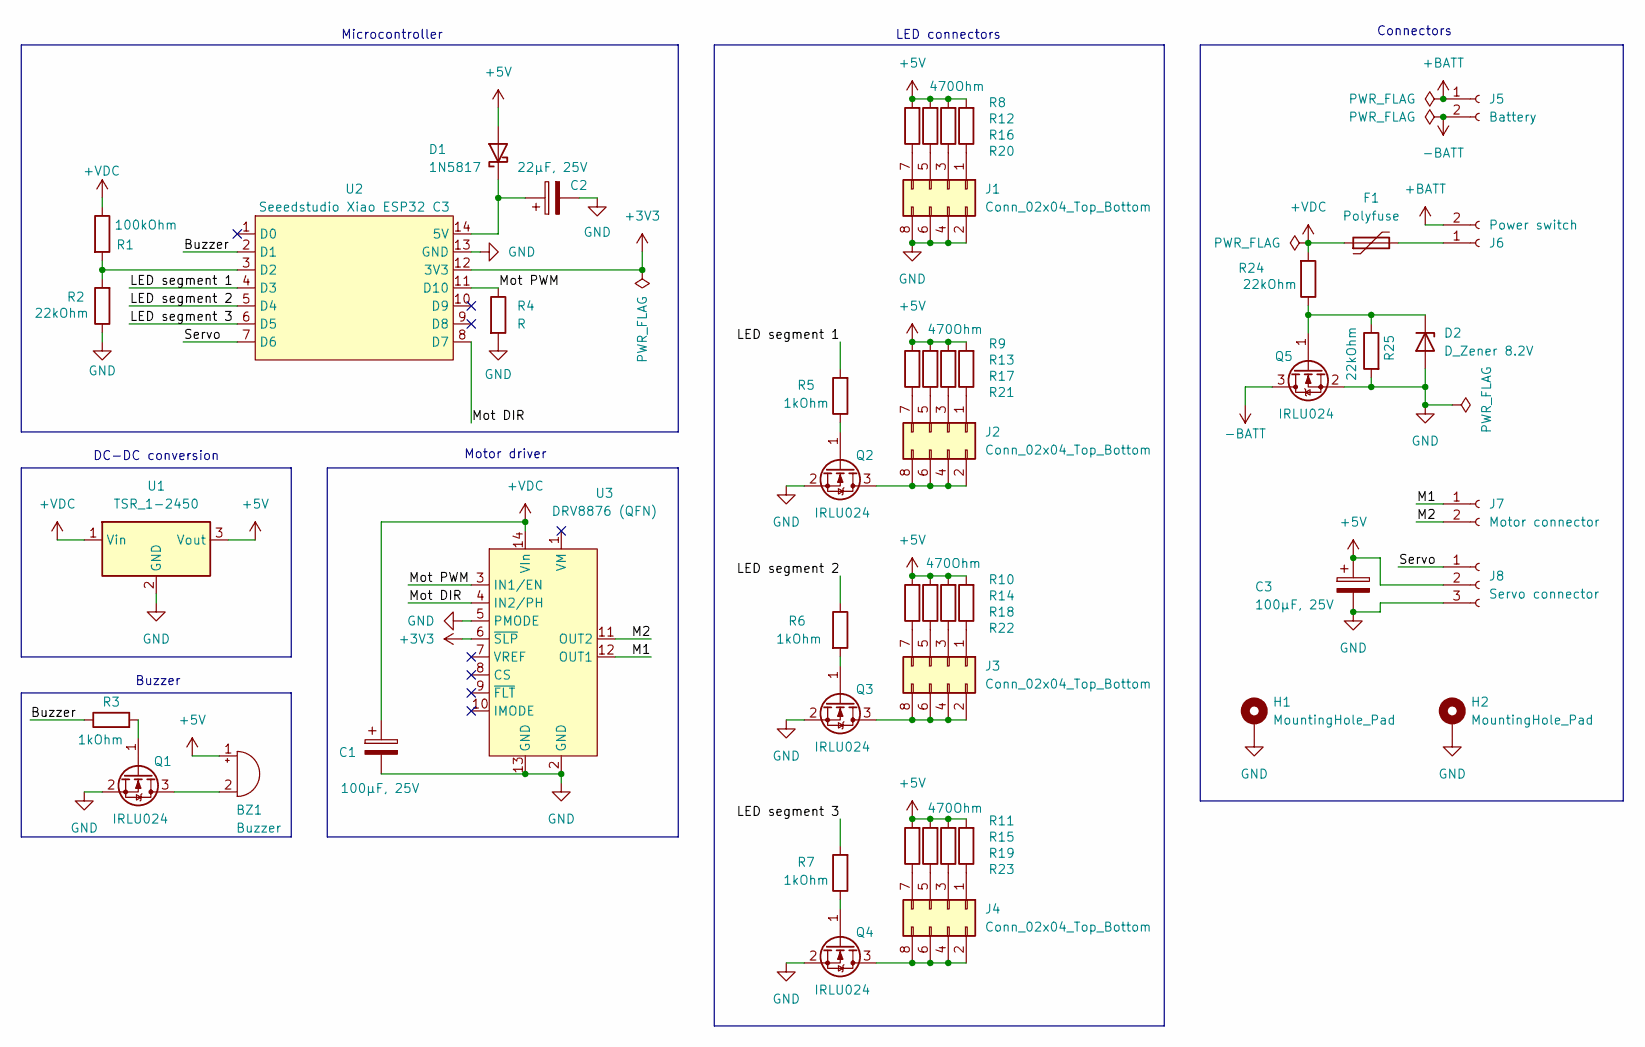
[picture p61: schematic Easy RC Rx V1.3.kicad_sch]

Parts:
BZ1: Buzzer; Buzzer 12mm 6.5mm spacing
C1, C3: 100µF, 25V; CP_Radial_D6.3mm_P2.50mm
C2: 22µF, 25V; CP_Radial_D5.0mm_P2.50mm
D1: 1N5817; D_DO-41_SOD81_P7.62mm_Horizontal
D2: D_Zener 8.2V; D_DO-41_SOD81_P7.62mm_Horizontal
F1: Polyfuse; ESKA FRG300-16F PTC Fuse
H1, H2: MountingHole_Pad; MountingHole_3.2mm_M3_DIN965_Pad_TopBottom
J1, J2, J3, J4: Conn_02x04_Top_Bottom; PinHeader_2x04_P2.54mm_Vertical
J5: Battery; PinHeader_1x02_P2.54mm_Vertical
J6: Power switch; PinHeader_1x02_P2.54mm_Vertical
J7: Motor connector; PinHeader_1x02_P2.54mm_Vertical
J8: Servo connector; PinHeader_1x03_P2.54mm_Vertical
Q1, Q2, Q3, Q4, Q5: IRLU024; TO-251-3_Vertical
R1: 100kOhm; R_Axial_DIN0207_L6.3mm_D2.5mm_P7.62mm_Horizontal
R2: 22kOhm; R_Axial_DIN0207_L6.3mm_D2.5mm_P7.62mm_Horizontal
R3, R5, R6, R7: 1kOhm; R_Axial_DIN0207_L6.3mm_D2.5mm_P2.54mm_Vertical
R4: R; R_Axial_DIN0207_L6.3mm_D2.5mm_P7.62mm_Horizontal
R8, R9, R10, R11, R12, R13, R14, R15, R16, R17, R18, R19, R20, R21, R22, R23: 470Ohm; R_Axial_DIN0207_L6.3mm_D2.5mm_P2.54mm_Vertical
R24, R25: 22kOhm; R_Axial_DIN0207_L6.3mm_D2.5mm_P2.54mm_Vertical
U1: TSR_1-2450; Converter_DCDC_TRACO_TSR-1_THT
U2: Seeedstudio Xiao ESP32 C3; Xiao ESP32C3
U3: DRV8876 (QFN); DRV8876(QFN)

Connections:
+3V3: U2.12 (3V3), U3.6 (~SLP)
+5V: BZ1.1 (+), C3.1, D1.2 (A), J8.2, R8.2, R9.2, R10.2, R11.2, R12.2, R13.2, R14.2, R15.2, R16.2, R17.2, R18.2, R19.2, R20.2, R21.2, R22.2, R23.2, U1.3 (Vout)
+BATT: J5.1, J6.2
+VDC: C1.1, F1.1, R1.1, R24.2, U1.1 (Vin), U3.14 (VIn)
-BATT: J5.2, Q5.3 (D)
/Buzzer: R3.1, U2.2 (D1)
/LED segment 1: R5.2, U2.4 (D3)
/LED segment 2: R6.1, U2.5 (D4)
/LED segment 3: R7.2, U2.6 (D5)
/M1: J7.1, U3.12 (OUT1)
/M2: J7.2, U3.11 (OUT2)
/Mot DIR: U2.8 (D7), U3.4 (IN2/PH)
/Mot PWM: R4.1, U2.11 (D10), U3.3 (IN1/EN)
/Servo: J8.1, U2.7 (D6)
GND: C1.2, C2.2, C3.2, D2.2 (A), H1.1, H2.1, J1.2, J1.4, J1.6, J1.8, J8.3, Q1.2 (S), Q2.2 (S), Q3.2 (S), Q4.2 (S), Q5.2 (S), R2.1, R4.2, R25.2, U1.2 (GND), U2.13 (GND), U3.2 (GND), U3.5 (PMODE), U3.13 (GND)
unnamed: BZ1.2 (-), Q1.3 (D)
unnamed: C2.1, D1.1 (K), U2.14 (5V)
unnamed: D2.1 (K), Q5.1 (G), R24.1, R25.1
unnamed: J1.1, R20.1
unnamed: J1.3, R16.1
unnamed: J1.5, R12.1
unnamed: J1.7, R8.1
unnamed: J2.1, R21.1
unnamed: J2.2, J2.4, J2.6, J2.8, Q2.3 (D)
unnamed: J2.3, R17.1
unnamed: J2.5, R13.1
unnamed: J2.7, R9.1
unnamed: J3.1, R22.1
unnamed: J3.2, J3.4, J3.6, J3.8, Q3.3 (D)
unnamed: J3.3, R18.1
unnamed: J3.5, R14.1
unnamed: J3.7, R10.1
unnamed: J4.1, R23.1
unnamed: J4.2, J4.4, J4.6, J4.8, Q4.3 (D)
unnamed: J4.3, R19.1
unnamed: J4.5, R15.1
unnamed: J4.7, R11.1
unnamed: F1.2, J6.1
unnamed: Q1.1 (G), R3.2
unnamed: Q2.1 (G), R5.1
unnamed: Q3.1 (G), R6.2
unnamed: Q4.1 (G), R7.1
unnamed: R1.2, R2.2, U2.3 (D2)

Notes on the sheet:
Buzzer
Microcontroller
LED connectors
DC-DC conversion
Connectors
Motor driver

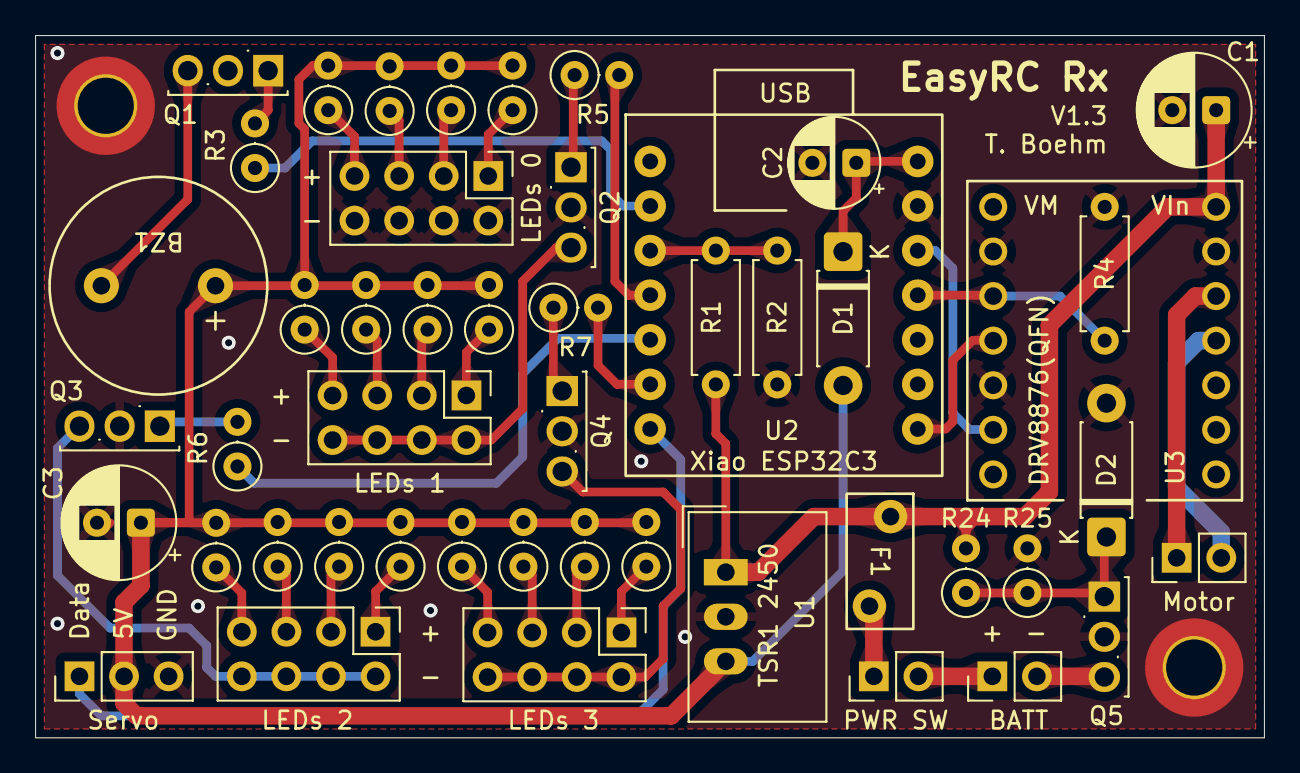
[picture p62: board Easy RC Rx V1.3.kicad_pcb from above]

Board: 2 copper layers, 70.0 x 40.0 mm, 50 parts (0 on the bottom side), 43 nets.

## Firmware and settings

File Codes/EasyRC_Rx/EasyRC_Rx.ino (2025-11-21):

//Libraries
#include <WiFi.h>
#include <esp_now.h> //library for bidirectional wireless communication between two ESP32
#include <esp_wifi.h> //needed to adjust the MAC address
#include <Wire.h>
#include <driver/ledc.h>

//Pin definitions
#define buzzer 3
#define vsense 4
#define led1 5
#define led2 6
#define led3 7 
#define pwm 10 
#define dir 20
#define servo 21

#define servoChannel 0
#define pwmChannel 1
#define ledChannel 2

//MAC addresses
uint8_t CarMAC[] = {0xAA, 0xA0, 0xBE, 0xEF, 0xFE, 0xED}; //we will set this MAC address for the car
uint8_t RemoteMAC[] = {0xB0, 0xAD, 0xBE, 0xEF, 0xFE, 0xEF}; //we will set this MAC address for the remote control
uint8_t broadMAC[] = {0xFF, 0xFF, 0xFF, 0xFF, 0xFF, 0xFF}; //using this MAC address as a receiver for sending packages means broadcasting (ignoring if the data has been received)

//global variables
int motorspeed = 0;
int motortimer = 0;
bool pwmconfig = 0;
int battimer = 0;
float batvolt = 0;
int batlow = 0;
int rctimer = 0;
int counter = 0;
bool afk = 0;
int serialtimer = 0;
int afktimer = 0;
int safetyloop = 0;
int indicatortimer = 0;
int ledstatus = 0;
int indicator = 0;
//ESP-NOW setup

//Structure to receive data; must match the sender structure of the RC!
typedef struct receive_message {
  int speed;
  int steer;
  bool horn;
  int motorint;
  int indicator;
  int brake;
} receive_message;

receive_message incoming;

// Callback when data is received
void OnDataRecv(const uint8_t * mac, const uint8_t *incomingData, int len) {
  bool sendercheck = true;
  for (int i = 0; i< 6; i++){ //When using ESP-NOW in broadcast mode, this code snippet ensures that only paired devices communicate with each other (verifying the sender's MAC address)
    if (mac[i] != RemoteMAC[i]){
      sendercheck = false;
      break;
    }
  }
  if (sendercheck){//&&len==13){ //only process the data if it is from the RC and if the packet has the correct length (data from the car to logger has a different length!)
    memcpy(&incoming, incomingData, sizeof(incoming));   
    rctimer = millis();  
  } 
}
esp_now_peer_info_t peerInfo; //make sure that the ESP-NOW lines are in the exact same order as in this sketch. Otherwise, there may be malfunctions.


void setup() {
  // put your setup code here, to run once:

Serial.begin(115200);

pinMode(buzzer, OUTPUT);
digitalWrite(buzzer, LOW);
pinMode(led1, OUTPUT);
digitalWrite(led1, HIGH);
pinMode(led2, OUTPUT);
digitalWrite(led2, LOW);
pinMode(led3, OUTPUT);
digitalWrite(led3, LOW);
pinMode(pwm, OUTPUT);
digitalWrite(pwm, LOW);
pinMode(dir, OUTPUT);
digitalWrite(dir, HIGH);
pinMode(servo, OUTPUT);
digitalWrite(servo, LOW);

ledc_timer_config_t timer_0;
  timer_0.speed_mode = LEDC_LOW_SPEED_MODE;
  timer_0.timer_num = LEDC_TIMER_0;
  timer_0.duty_resolution = LEDC_TIMER_12_BIT; // Servo: 12 Bit
  timer_0.freq_hz = 50;
  timer_0.clk_cfg = LEDC_AUTO_CLK;
ledc_timer_config(&timer_0);

ledc_channel_config_t ch0;
  ch0.gpio_num = servo;
  ch0.speed_mode = LEDC_LOW_SPEED_MODE;
  ch0.channel = LEDC_CHANNEL_0;
  ch0.intr_type = LEDC_INTR_DISABLE;
  ch0.timer_sel = LEDC_TIMER_0;
  ch0.duty = 0;
  ch0.hpoint = 0;
ledc_channel_config(&ch0);

  // Activate ESP-NOW
  WiFi.mode(WIFI_STA); //Set device as a Wi-Fi Station
  esp_wifi_set_mac(WIFI_IF_STA, CarMAC); //Overwrite hardware MAC with this new MAC address
  esp_wifi_set_protocol(WIFI_IF_STA, WIFI_PROTOCOL_LR);

  esp_now_init(); // Initialize ESP-NOW

  // Register peer
  memcpy(peerInfo.peer_addr, broadMAC, 6);
  esp_now_add_peer(&peerInfo); // Add peer 

  esp_wifi_set_promiscuous(true); //set WiFi channel
  esp_wifi_set_channel(1, WIFI_SECOND_CHAN_NONE);
  esp_wifi_set_promiscuous(false);     
  peerInfo.channel = 1;  
  peerInfo.encrypt = false;

  // Register for a callback function that will be called when data is received
  esp_now_register_recv_cb(esp_now_recv_cb_t(OnDataRecv));

  digitalWrite(led2,HIGH);
  digitalWrite(led3,HIGH);
  setPWMchannel(buzzer,250); //startup buzzer sequence
  Buzzer(true);
  delay(100);
  Buzzer(false);
  delay(400);
  Buzzer(true);
  delay(100);
  Buzzer(false);
  delay(400);
  setPWMchannel(buzzer,350);
  Buzzer(true);
  delay(500);
  Buzzer(false);
  delay(1000);
  setPWMchannel(buzzer,400);
  digitalWrite(led2,LOW);
  digitalWrite(led3,LOW);

  while(rctimer==0&&batlow<500){ //indicate "waiting for connection" with beeping every 2 s
    checkBattery();
    delay(10);
    counter = counter + 1;
    if(counter>199){
      Buzzer(false);
      digitalWrite(led2,LOW);
      digitalWrite(led3,LOW);
      counter = 0;
    }else if(counter>179){
      Buzzer(true);
      digitalWrite(led2,HIGH);   
      digitalWrite(led3,HIGH);    
    }
  }

  counter = 0;

  if(rctimer>0){ //connection established sequence
    digitalWrite(led2, HIGH);
    digitalWrite(led3, HIGH);
    setPWMchannel(buzzer,350);
    Buzzer(true);
    delay(400);
    Buzzer(false);
    delay(100);
    setPWMchannel(buzzer,500);
    Buzzer(true);
    delay(200);
    Buzzer(false);
    digitalWrite(led2, LOW);
    digitalWrite(led3, LOW);
  }

  serialtimer = millis();
  afktimer = millis();
  motortimer = millis();
  indicatortimer = millis();

}

void loop() {
  checkBattery();
  checkUser();

  if(millis()>rctimer+999||batlow>9999||afk==1){ //stop motor and beep if an error occurs
    safetyloop = 1;
    ServoControl(0);
    motorspeed = setMotorSpeed(0, motorspeed);
    if(motorspeed!=0){
      MotorControl(motorspeed);
    }else{
      if(pwmconfig==0){
        setPWMchannel(buzzer,400);
      }
      if (afk==1){
        if(millis()>battimer+3000){
          battimer = millis();
          digitalWrite(led2,LOW);
          digitalWrite(led3,LOW);
          Buzzer(false);
        }else if(millis()>battimer+2000){
          digitalWrite(led2,HIGH);
          digitalWrite(led3,HIGH);
          Buzzer(true);
        }      
      }else if(batlow>9999){
        if(millis()>battimer+3000){
          battimer = millis();
          digitalWrite(led2,LOW);
          digitalWrite(led3,LOW);
          Buzzer(false);
        }else if(millis()>battimer+2500){
          digitalWrite(led2,HIGH);
          digitalWrite(led3,HIGH);
          Buzzer(true);
        }           
      }else{
        if(millis()>battimer+3000){
          battimer = millis();
          digitalWrite(led2,LOW);
          digitalWrite(led3,LOW);
          Buzzer(false);
        }else if(millis()>battimer+1500){
          digitalWrite(led2,HIGH);
          digitalWrite(led3,HIGH);
          Buzzer(true);
        }   
      }

    } 
    if(batlow>2499){
      Serial.println("Battery low!");
    }else if(millis()>rctimer+999){
      Serial.println("No connection");
    }else if(afk==1){
      Serial.println("No user input!");
    }

  }else{
    ServoControl(incoming.steer);
    motorspeed = setMotorSpeed(incoming.speed, motorspeed);  
    if (incoming.brake==1){
      digitalWrite(led1,HIGH);
    }else if(ledstatus<2){
      digitalWrite(led1,LOW);
      ledstatus=ledstatus+1;
    }else{
      digitalWrite(led1,HIGH);
      ledstatus=0;
    }
    if(indicator!=incoming.indicator){
      indicatortimer = millis()-501;
      digitalWrite(led2,LOW);
      digitalWrite(led3,LOW);      
    }
    if (millis()>indicatortimer + 1000){
      indicatortimer = millis();
      digitalWrite(led2,LOW);
      digitalWrite(led3,LOW);
    }else if(millis()>indicatortimer + 500){
      if(incoming.indicator==1){
        digitalWrite(led2,HIGH);
        digitalWrite(led3,LOW);
      }else if(incoming.indicator==2){
        digitalWrite(led3,HIGH);
        digitalWrite(led2,LOW);
      }
    }
    indicator = incoming.indicator;
    safetyloop = 0;
   }

  if (safetyloop==0){
    if(motorspeed==0){
      if (incoming.horn==1&&pwmconfig==0){ //switch PWM from motor to buzzer if the horn is requested at standstill
        setPWMchannel(buzzer,400);
      }else{
        if (incoming.horn){
          Buzzer(true);
        }else{
          Buzzer(false);
        }
      }
    }else{
      if(pwmconfig==1){
        setPWMchannel(pwm,20000);
      }else{
        MotorControl(motorspeed);
        //MotorControl(incoming.speed);
      }
    }
  }


  if(millis()>serialtimer+1000){
    Serial.print("Speed: ");
    Serial.println(incoming.speed);
    Serial.print("Motor speed: ");
    Serial.println(motorspeed);
    Serial.print("Steering: ");
    Serial.println(incoming.steer);
    Serial.print("Horn: ");
    Serial.println(incoming.horn);
    Serial.print("Battery voltage: ");
    Serial.println(batvolt);
    Serial.println("----------");
    serialtimer = millis();
  }

}

void checkUser(){
  if(incoming.speed==0&&incoming.horn==0){ //if neither the horn or the motor is operated for approx. 1 min (assuming a loop time of 5 ms), the user is probably away from keyboard - triggers a warning
    if(millis()>afktimer+60000){
      afk=1;
    }
  }else{
    afktimer = millis();
    afk = 0;
  }
}

void checkBattery(){
  if (batlow<10000){ //low battery warning circuit
    batvolt = analogReadMilliVolts(vsense);
    batvolt = (batvolt/1000)*(100+22)/22; //voltage divider: 100kOhm + 22kOhm
    if (batvolt<10.2){
      batlow = batlow + 1;
    }else if(batlow>0){
      batlow = batlow - 1;
    }
  }
}

int setMotorSpeed(int newval, int oldval){
  int outputval = 0;
  if(millis()>motortimer+incoming.motorint){

    motortimer = millis();
    
    if (oldval<10&&oldval>-10){ //select motor spin direction: only change at speeds close to 0
      if (newval<0){
        digitalWrite(dir, LOW);
      }else{
        digitalWrite(dir, HIGH);
      }
    }

    if(newval>oldval){
      if (newval>oldval+10){
        outputval = oldval + 5;
      }else if (newval>oldval+5){
        outputval = oldval + 2;
      }else if (newval>oldval){
        outputval = oldval + 1;
      }
    }else if(newval<oldval){
      if (newval<oldval-10){
        outputval = oldval - 5;
      }else if (newval<oldval-5){
        outputval = oldval - 2;
      }else if (newval<oldval){
        outputval = oldval - 1;
      }      
    }else{
      outputval = oldval;
    }  
  }else{
    outputval = oldval;
  }

  return outputval;
}

void setPWMchannel(int pinNumber, int frequency){

  ledc_timer_config_t timer_1;
    timer_1.speed_mode = LEDC_LOW_SPEED_MODE;
    timer_1.timer_num = LEDC_TIMER_1;
    timer_1.duty_resolution = LEDC_TIMER_8_BIT; // Servo: 12 Bit
    timer_1.freq_hz = frequency;
    timer_1.clk_cfg = LEDC_AUTO_CLK;
  ledc_timer_config(&timer_1);

  ledc_channel_config_t ch1;
    ch1.gpio_num = pinNumber;
    ch1.speed_mode = LEDC_LOW_SPEED_MODE;
    ch1.channel = LEDC_CHANNEL_1;
    ch1.intr_type = LEDC_INTR_DISABLE;
    ch1.timer_sel = LEDC_TIMER_1;
    ch1.duty = 0;
    ch1.hpoint = 0;
  ledc_channel_config(&ch1); 

  if (pinNumber==pwm){ //reset pin usage of the other PWM channel
    pinMode(buzzer,OUTPUT);
    digitalWrite(buzzer,LOW);
    pwmconfig=0;
    Serial.println("Now switching to drivng!");
  }else{
    pinMode(pwm,OUTPUT);
    digitalWrite(pwm,LOW);
    pwmconfig=1;
    Serial.println("Now switching to honking!");    
  }
  delay(10);

}

void ServoControl(int DutyCycle){
   ledc_set_duty(LEDC_LOW_SPEED_MODE, LEDC_CHANNEL_0,DutyCycle);
   ledc_update_duty(LEDC_LOW_SPEED_MODE,LEDC_CHANNEL_0);   
}

void MotorControl(int DutyCycle){
  if(pwmconfig==0){
    ledc_set_duty(LEDC_LOW_SPEED_MODE, LEDC_CHANNEL_1,abs(DutyCycle));
    ledc_update_duty(LEDC_LOW_SPEED_MODE,LEDC_CHANNEL_1);
  }
}

void Buzzer(bool on){
  if(pwmconfig==1){ //prevent motor pwm outputs upon buzzer calling by checking the pwm channel configuration
    if(on){
      ledc_set_duty(LEDC_LOW_SPEED_MODE, LEDC_CHANNEL_1,127);
      ledc_update_duty(LEDC_LOW_SPEED_MODE,LEDC_CHANNEL_1); 
    }else{
      ledc_set_duty(LEDC_LOW_SPEED_MODE, LEDC_CHANNEL_1,0);
      ledc_update_duty(LEDC_LOW_SPEED_MODE,LEDC_CHANNEL_1); 
    }
  }
}

float readVoltage(){
  float val = 0;
  val = analogReadMilliVolts(vsense);
  val = (val/1000)*(100+22)/22;
  return val;
}

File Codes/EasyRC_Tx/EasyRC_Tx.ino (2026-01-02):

//Libraries
#include <WiFi.h>
#include <esp_now.h> //library for bidirectional wireless communication between two ESP32
#include <esp_wifi.h> //needed to adjust the MAC address
#include <Wire.h>

//Pin definitions
#define vsense 2
#define joyx 3
#define joyy 4 
#define button 5 
#define led 20

//calibration data
bool motordirection = false; //change this variable to false to invert the motor spin direction 
int motorint = 10; //sets the delay time between motor speed changes (in ms). Higher values result in 
//better traction but slower responses. Values between 5 and 10 are recommended.
int speedlimit = 127; //this variable sets the maximum speed of the car (values between 0 and 255)
int leftlimit = 358; //steering limit calculation: leftlimit = x/20ms*2^12 (default: 205 (x = 1ms))
int rightlimit = 258; //steering limit calculation: rightlimit = x/20ms*2^12 (default: 410 (x = 2ms))
//RC servos run at 50 Hz (20 ms intervals), with the center at 1.5 ms and a range of +-0.5 ms around the center
//starting values should be 205 to 410 (left to right or right to left, depends on the servo)
//adjust these values to a smaller or larger interval depending on the actual steering angles
//individually decrease/increase one of the two values to trim the center of the steering

//MAC addresses
uint8_t CarMAC[] = {0xAA, 0xA0, 0xBE, 0xEF, 0xFE, 0xED}; //we will set this MAC address for the car
uint8_t RemoteMAC[] = {0xB0, 0xAD, 0xBE, 0xEF, 0xFE, 0xEF}; //we will set this MAC address for the remote control
uint8_t broadMAC[] = {0xFF, 0xFF, 0xFF, 0xFF, 0xFF, 0xFF}; //using this MAC address as a receiver for sending 
//packages means broadcasting (ignoring if the data has been received)

//global variables
int speed = 0;
int steer = 0;
int rctimer = 0;
int battimer = 0;
float batvolt = 0;
int batlow = 0;
int speedcenter = 0;
int steercenter = 0;
int analogspeed = 0;
int analogsteer = 0;


//ESP-NOW setup
/*
  Rui Santos & Sara Santos - Random Nerd Tutorials
  Complete project details at https://RandomNerdTutorials.com/esp-now-two-way-communication-esp32/
  Permission is hereby granted, free of charge, to any person obtaining a copy of this software and associated documentation files.
  The above copyright notice and this permission notice shall be included in all copies or substantial portions of the Software.
*/

// Structure to send data; must match the receiver structure of the car!
typedef struct send_message {
  int speed;
  int steer;
  bool horn;
  int motorint;
  int indicator;
  int brake;
} send_message;

// Create a structured object
send_message outgoing;

esp_now_peer_info_t peerInfo; //make sure that the ESP-NOW lines are in the exact same order as in this sketch. Otherwise, there may be malfunctions.

void setup() {
  // put your setup code here, to run once:

  for (int i = 0; i<10; i++){
    speed = speed + analogRead(joyx);
    steer = steer + analogRead(joyy);

    speedcenter = speed/10;
    steercenter = steer/10;
  }

  pinMode(led,OUTPUT);
  digitalWrite(led,HIGH);
  pinMode(button,INPUT_PULLUP);

  // Activate ESP-NOW
  WiFi.mode(WIFI_STA); //Set device as a Wi-Fi Station
  esp_wifi_set_mac(WIFI_IF_STA, RemoteMAC); //Overwrite hardware MAC with this new MAC address
  esp_wifi_set_protocol(WIFI_IF_STA, WIFI_PROTOCOL_LR); //the long range WiFI protocol should theoretically improve the max. distance of the wireless connection (not verified)
  esp_now_init(); // Initialize ESP-NOW

  esp_wifi_set_promiscuous(true); //set WiFi channel
  esp_wifi_set_channel(1, WIFI_SECOND_CHAN_NONE);
  esp_wifi_set_promiscuous(false);     
  peerInfo.channel = 1;  
  peerInfo.encrypt = false;  

  memcpy(peerInfo.peer_addr, broadMAC, 6); //data is sent in broadcast mode: sent to all listening devices
  esp_now_add_peer(&peerInfo); // Add peer   

  outgoing.motorint = motorint;

  rctimer = millis();
  battimer = millis();

  Serial.begin(115200);

}

void loop() {
  // put your main code here, to run repeatedly:

  readXaxis();
  readYaxis();
  checkBattery();

  if(digitalRead(button)){
    outgoing.horn = false;
  }else{
    outgoing.horn = true;
  }

  if (millis()>rctimer+49){ //send a new data package every 50 ms (20 times per second)
    rctimer = millis(); 
    esp_now_send(broadMAC, (uint8_t *) &outgoing, sizeof(outgoing));
    SerialOutput();
  }

}

void readXaxis(){
  speed = analogRead(joyx);
  analogspeed = speed;
  if (speed>speedcenter-200&&speed<speedcenter+200){ //sets +-5% from the center value of the joystick as zero
    speed = speedcenter;
  }
  if (speed<speedcenter-1750){
    speed = speedcenter-1750;
  }else if(speed>speedcenter + 1750){
    speed = speedcenter + 1750;
  }
  if(speed>speedcenter){
    speed = map(speed,speedcenter+100,speedcenter+1750,speedcenter,speedcenter+1750);
  }else if(speed<speedcenter){
    speed = map(speed,speedcenter-100,speedcenter-1750,speedcenter,speedcenter-1750);
  }

  if (motordirection){
    speed = map(speed,speedcenter-1750,speedcenter+1750,-speedlimit,speedlimit);
  }else{
    speed = map(speed,speedcenter-1750,speedcenter+1750,speedlimit,-speedlimit);
  }
  outgoing.speed = speed;
  if (motordirection){
    if (speed<=0){
      outgoing.brake = 1;
    }else{
      outgoing.brake = 0;
    }
  }else{
    if (speed>=0){
      outgoing.brake = 1;
    }else{
      outgoing.brake = 0;
    }  
  }
}

void readYaxis(){
  steer = analogRead(joyy);
  analogsteer = steer;
  if (steer>steercenter-150&&steer<steercenter+150){ //sets +-5% from the center value of the joystick as zero
    steer = steercenter;
  }
  if (steer<steercenter-1750){
    steer = steercenter-1750;
  }else if(steer>steercenter + 1750){
    steer = steercenter + 1750;
  }
  if(steer>steercenter){
    steer = map(steer,steercenter+150,steercenter+1750,steercenter,steercenter+1750);
  }else if(steer<steercenter){
    steer = map(steer,steercenter-150,steercenter-1750,steercenter,steercenter-1750);
  }

  steer = map(steer,steercenter-1750,steercenter+1750,leftlimit,rightlimit);
  outgoing.steer = steer;  
  if (leftlimit>rightlimit){
    if(steer>(leftlimit+rightlimit)/2+5){
      outgoing.indicator = 1;
    }else if(steer<(leftlimit+rightlimit)/2-5){
      outgoing.indicator = 2;
    }else{
      outgoing.indicator = 0;
    }
  }else{
    if(steer<(leftlimit+rightlimit)/2-5){
      outgoing.indicator = 1;
    }else if(steer>(leftlimit+rightlimit)/2+5){
      outgoing.indicator = 2;
    }else{
      outgoing.indicator = 0;
    }    
  }
}

void checkBattery(){
  if (batlow<500){ //low battery warning circuit
    batvolt = analogReadMilliVolts(vsense);
    batvolt = (batvolt/1000)*(33+33)/33; //voltage divider: 33kOhm + 33kOhm equals measured voltage times 2
    if (batvolt<3.4){
      batlow = batlow + 1;
    }else if(batlow>0){
      batlow = batlow - 1;
    }
  }else{
    if(millis()>battimer+500){
      battimer = millis();
      digitalWrite(led,LOW);
    }else if(millis()>battimer+250){
      digitalWrite(led,HIGH);
    }
  }
}
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

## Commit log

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2026-01-02 Update and rename CAD files/Remote control battery cover.step to CAD files/Remote control/Remote control battery cover.step
    [Remote control battery cover.step]
2026-01-02 Update and rename CAD files/10teeth crown gear.step to CAD files/Car/10teeth crown gear.step
    [10teeth crown gear.step]
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2026-01-02 Update and rename Easy RC Rx.kicad_pcb to Rx V1.2.kicad_pcb
    [Rx V1.2.kicad_pcb]
2026-01-02 Update and rename Easy RC Rx.kicad_sch to Rx V1.2.kicad_sch
    [Rx V1.2.kicad_sch]
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2026-01-09 Update and rename Servo horn attachment large.step to Servo horn attachment large TPU.step
    [Servo horn attachment large TPU.step]
2026-01-09 Update and rename Servo horn attachment small.step to Servo horn attachment small TPU.step
    [Servo horn attachment small TPU.step]
2026-01-09 Update and rename Right rear axle.step to Right rear axle TPU.step
    [Right rear axle TPU.step]
2026-01-09 Update and rename Left rear axle.step to Left rear axle TPU.step
    [Left rear axle TPU.step]
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2026-01-09 Update and rename Rx PCB/KiCAD files/Rx V1.2.kicad_pcb to PCBs/EasyRC rx/KiCAD files/Rx V1.2.kicad_pcb
    [Rx V1.2.kicad_pcb]
2026-01-09 Update and rename Rx V1.2.kicad_pcb to Rx V1.2.kicad_pcb
    [Rx V1.2.kicad_pcb]
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2026-01-09 Update and rename Rx PCB/KiCAD files/Rx V1.2.kicad_sch to PCBs/EasyRC Rx/KiCAD files/Rx V1.2.kicad_sch
    [Rx V1.2.kicad_sch]
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2026-01-09 Update and rename Tx PCB/KiCAD files/Tx V1.1.kicad_pcb to PCBs/EasyRC Tx/KiCAD files/Tx V1.1.kicad_pcb
    [Tx V1.1.kicad_pcb]
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2026-01-09 Update and rename Tx PCB/KiCAD files/Tx V1.1.kicad_sch to PCBs/EasyRC Tx/KiCAD files/Tx V1.1.kicad_sch
    [Tx V1.1.kicad_sch]
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2026-04-11 Rename CAD files/Assembly/Easy RC remote control.step to Legacy/CAD files/Assembly/Easy RC remote control.step
    [Easy RC remote control.step]
2026-04-11 Rename CAD files/Car/10teeth crown gear.step to Legacy/CAD files/Car/10teeth crown gear.step
    [10teeth crown gear.step]
2026-04-11 Rename CAD files/Car/15teeth crown gear.step to Legacy/CAD files/Car/15teeth crown gear.step
    [15teeth crown gear.step]
2026-04-11 Rename CAD files/Car/16 teeth bearing mount.step to Legacy/CAD files/Car/16 teeth bearing mount.step
    [16 teeth bearing mount.step]
2026-04-11 Rename CAD files/Car/16 teeth gear.step to Legacy/CAD files/Car/16 teeth gear.step
    [16 teeth gear.step]
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2026-04-11 Rename CAD files/Car/Front rim locking ring.step to Legacy/CAD files/Car/Front rim locking ring.step
    [Front rim locking ring.step]
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2026-04-11 Rename CAD files/Car/Front wheel mount spacer.step to Legacy/CAD files/Car/Front wheel mount spacer.step
    [Front wheel mount spacer.step]
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2026-04-11 Rename CAD files/Car/Left front wheel mount.step to Legacy/CAD files/Car/Left front wheel mount.step
    [Left front wheel mount.step]
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2026-04-11 Rename CAD files/Car/Left rear LED insert.step to Legacy/CAD files/Car/Left rear LED insert.step
    [Left rear LED insert.step]
2026-04-11 Rename CAD files/Car/Left rear axle TPU.step to Legacy/CAD files/Car/Left rear axle TPU.step
    [Left rear axle TPU.step]
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2026-04-11 Rename CAD files/Car/Right front wheel mount.step to Legacy/CAD files/Car/Right front wheel mount.step
    [Right front wheel mount.step]
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2026-04-11 Rename CAD files/Car/Right rear LED insert.step to Legacy/CAD files/Car/Right rear LED insert.step
    [Right rear LED insert.step]
2026-04-11 Rename CAD files/Car/Right rear axle TPU.step to Legacy/CAD files/Car/Right rear axle TPU.step
    [Right rear axle TPU.step]
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2026-04-11 Rename CAD files/Car/Servo horn attachment large TPU.step to Legacy/CAD files/Car/Servo horn attachment large TPU.step
    [Servo horn attachment large TPU.step]
2026-04-11 Rename CAD files/Car/Servo horn attachment small TPU.step to Legacy/CAD files/Car/Servo horn attachment small TPU.step
    [Servo horn attachment small TPU.step]
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2026-04-11 Rename CAD files/Remote control/Remote control battery cover.step to Legacy/CAD files/Remote control/Remote control battery cover.step
    [Remote control battery cover.step]
2026-04-11 Rename CAD files/Remote control/Remote control bottom.step to Legacy/CAD files/Remote control/Remote control bottom.step
    [Remote control bottom.step]
2026-04-11 Rename CAD files/Remote control/Remote control joystick extension.step to Legacy/CAD files/Remote control/Remote control joystick extension.step
    [Remote control joystick extension.step]
2026-04-11 Rename CAD files/Remote control/Remote control lower intermediate frame.step to Legacy/CAD files/Remote control/Remote control lower intermediate frame.step
    [Remote control lower intermediate frame.step]
2026-04-11 Rename CAD files/Remote control/Remote control top.step to Legacy/CAD files/Remote control/Remote control top.step
    [Remote control top.step]
2026-04-11 Rename CAD files/Remote control/Remote control upper intermediate frame.step to Legacy/CAD files/Remote control/Remote control upper intermediate frame.step
    [Remote control upper intermediate frame.step]
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
